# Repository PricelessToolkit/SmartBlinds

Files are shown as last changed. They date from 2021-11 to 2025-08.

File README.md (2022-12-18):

# Battery Powered Smart Blinds
 
With lithium-ion battery 2500 mA autonomy is 8 months.

## Youtube Video

https://youtu.be/99Hgh3yqyf8

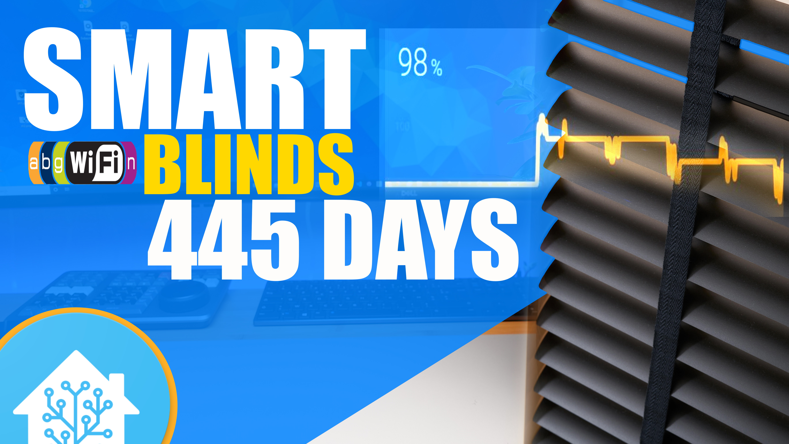
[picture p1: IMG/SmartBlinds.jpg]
SmartBlinds (https://youtu.be/99Hgh3yqyf8)


### Want to support me ? Subscribe and like!

# Update

15.11.2021 - v2 board, I added D5,D6,D7 pins for manual control."not tested" 
the board has become a little bigger, it will not fit into the case. You need to change the 3d model.

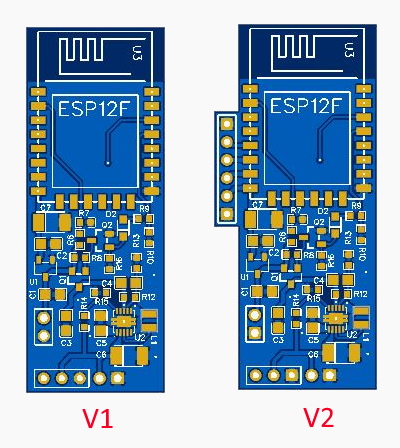
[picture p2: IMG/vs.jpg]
SmartBlinds
[]

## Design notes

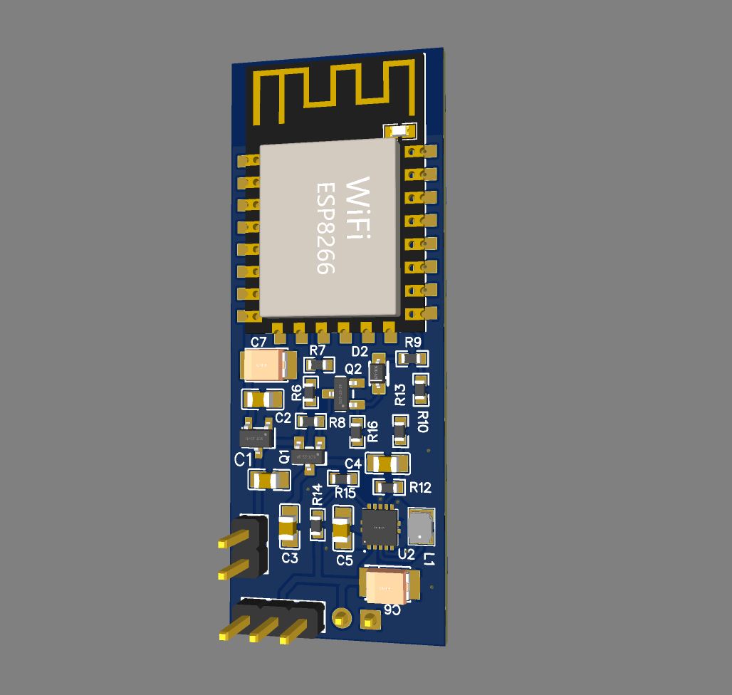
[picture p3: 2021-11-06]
IMG/v1.JPG

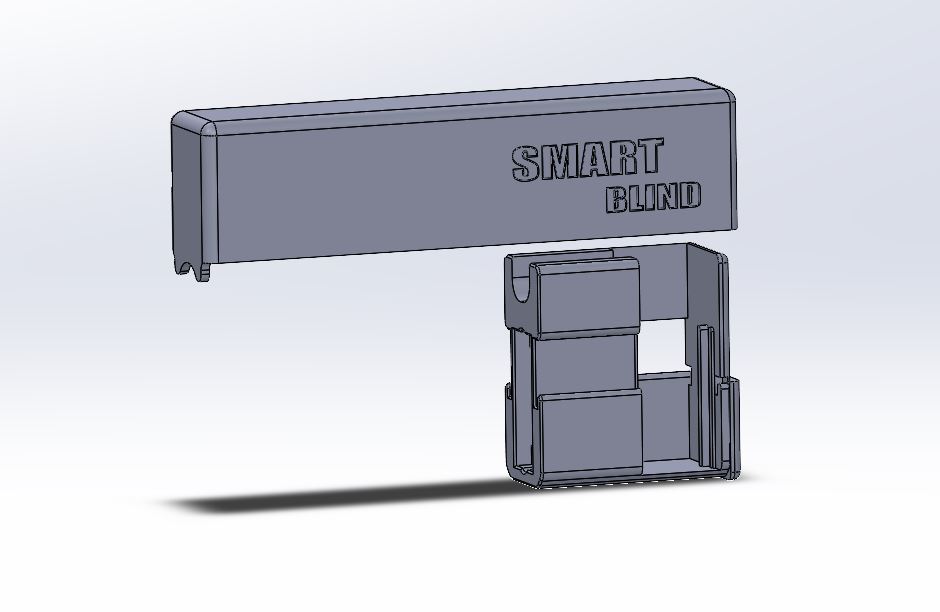
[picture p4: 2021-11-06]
IMG/SB.JPG

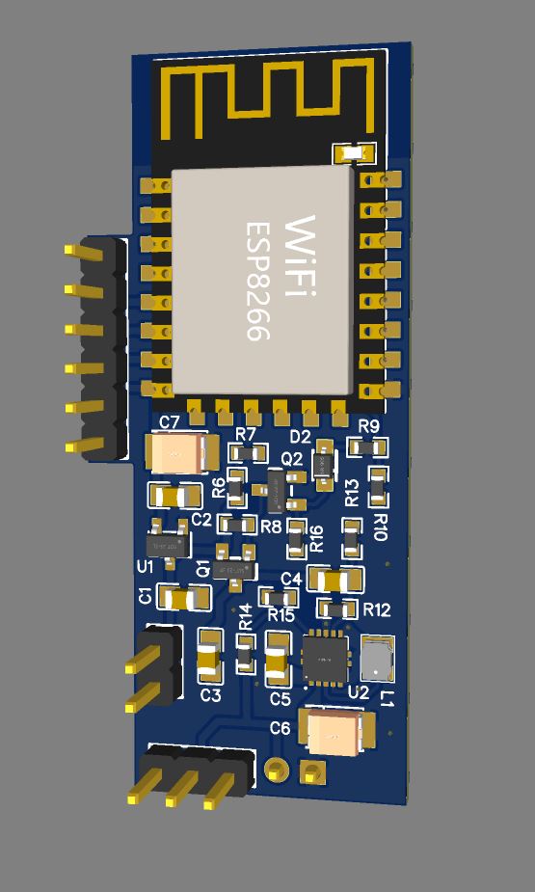
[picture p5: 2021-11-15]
IMG/v2.JPG

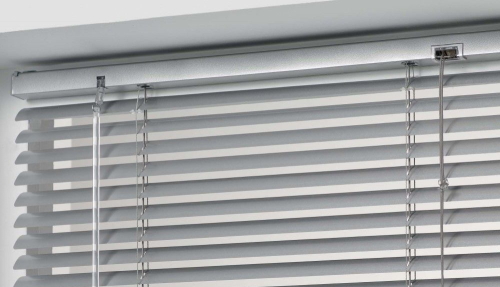
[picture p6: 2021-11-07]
IMG/Blinds.jpg

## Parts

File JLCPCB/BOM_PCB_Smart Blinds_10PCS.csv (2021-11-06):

ID | Name | Designator | Footprint | Quantity | Manufacturer Part | Manufacturer | Supplier | Supplier Part | Price | Pins | 3DModel | Assembly Type | JLCPCB Part Class | JLCPCB SMD | LCSC Assembly | Paste Type | Contributor | SMT Type | image | link
2 | 10k | R1,R2,R3,R4,R5,R9 | R0603 | 60 | RTT03103JTP | RALEC | LCSC | C103210 | 0.001 | 2 | R0603_L1.6-W0.8-H0.8 |  |  |  |  |  | LCEDA_Lib |  |  | https://www.mouser.in/datasheet/2/447/PYu_RT_1_to_0_01_RoHS_L_11-1669912.pdf
3 | TS342A2P-WZ | PROG,RST | SW-SMD_L4.0-W2.9-LS5.0 | 20 | TS342A2P-WZ | SHOU HAN | LCSC | C557591 | 0.041 | 2 |  |  | Extended Part |  |  |  | LCSC |  |  | https://item.szlcsc.com/330471.html
4 | ESP-12F(ESP8266MOD) | U3 | WIFIM-SMD_ESP-12F-ESP8266MOD | 10 | ESP-12F(ESP8266MOD) | Ai-Thinker | LCSC | C82891 | 1.482 | 22 | WIFIM-SMD_WIFI-L24.0-W16.0-H3.1 |  | Extended Part |  |  |  | 立创EDA官方封装库 |  |  | https://item.szlcsc.com/84052.html
5 | 10uf | C7 | CASE-B_3528 | 10 | T491A226K006AT | KEMET | LCSC | C118989 | 0.129 | 2 | CASE-B_L3.5-W2.8-H1.9 |  |  |  |  |  | LCEDA_Lib |  |  | https://img.jlc.com/pdf/applyPasteComponent/2021-05-29/507681S/b3196547ade04cd291a1b09ea1ee2ece/C7199_22UF.PDF
6 | 100nF | C2,C1 | C0805 | 20 | C0805B104M500NT | 火炬 | LCSC | C515949 | 0.007 | 2 | C0805_L2.0-W1.3-H1.3 |  |  |  |  |  | LCEDA_Lib |  |  | https://item.szlcsc.com/373011.html
7 | 10uF | C3 | C0805 | 10 | GRM155R61A106ME21D | Murata Electronics | LCSC | C324476 | 0.021 | 2 | C0805_L2.0-W1.3-H1.3 |  |  |  |  |  | LCEDA_Lib |  |  | https://item.szlcsc.com/373011.html
8 | 0.1uF | C4,C5 | C0805 | 20 | C0805B104M500NT | 火炬 | LCSC | C515949 | 0.007 | 2 | C0805_L2.0-W1.3-H1.3 |  |  |  |  |  | LCEDA_Lib |  |  | https://item.szlcsc.com/373011.html
9 | 1N5819 | D2 | SOD-323_L1.8-W1.3-LS2.5-RD | 10 | 1N5819WS(SL) | KEXIN | LCSC | C489147 | 0.026 | 2 | SOD-323_L1.7-W1.3-H1.1-LS2.5 |  |  |  |  |  | LCSC |  |  | https://item.szlcsc.com/295156.html
10 | 4.7uH | L1 | IND-SMD_L2.5-W2.0_WPN2520X | 10 | WPN252010H4R7MT | Sunlord | LCSC | C97033 | 0.061 | 2 | IND-SMD_L2.5-W2.0-H1.0_WPN2520X |  | Extended Part |  |  |  | 立创EDA官方封装库 |  |  | https://item.szlcsc.com/98236.html
11 | AO3401A | Q1 | SOT-23_L2.9-W1.3-P1.90-LS2.4-BR | 10 | AO3401A | AOS | LCSC | C15127 | 0.161 | 3 | SOT-23-3P_L2.9-W1.3-H1.0-LS2.4-P0.95 | smtWeld |  | Yes |  | base | 官方封装库 | Basic | //image.lceda.cn/szlcsc/C15127.jpg | https://item.szlcsc.com/236142.html
12 | 2n3904S | Q2 | SOT-23-3_L2.9-W1.3-P1.90-LS2.4-TR | 10 | 2n3904S-RTK/PS | KEC | LCSC | C18536 | 0.014 | 3 | SOT-23-3P_L2.9-W1.3-H1.0-LS2.4-P0.95 | smtWeld |  | Yes | Yes | expand | 立创EDA官方封装库 | Extend | //image.lceda.cn/szlcsc/C18536.jpg | https://item.szlcsc.com/70837.html
13 | 100k | R6,R8,R16 | R0603 | 30 | RTT03104JTP | RALEC | LCSC | C103211 | 0.001 | 2 | R0603_L1.6-W0.8-H0.8 |  |  |  |  |  | LCEDA_Lib |  |  | https://www.mouser.in/datasheet/2/447/PYu_RT_1_to_0_01_RoHS_L_11-1669912.pdf
14 | 20k | R7 | R0603 | 10 | RTT03203JTP | RALEC | LCSC | C103397 | 0.003 | 2 | R0603_L1.6-W0.8-H0.8 |  |  |  |  |  | LCEDA_Lib |  |  | https://www.mouser.in/datasheet/2/447/PYu_RT_1_to_0_01_RoHS_L_11-1669912.pdf
15 | 220k | R10,R13,R15 | R0603 | 30 | RTT03224JTP | RALEC | LCSC | C103427 | 0.002 | 2 | R0603_L1.6-W0.8-H0.8 |  |  |  |  |  | LCEDA_Lib |  |  | https://www.mouser.in/datasheet/2/447/PYu_RT_1_to_0_01_RoHS_L_11-1669912.pdf
16 | 2M | R12,R14 | R0603 | 20 | RTT03205JTP | RALEC | LCSC | C103403 | 0.001 | 2 | R0603_L1.6-W0.8-H0.8 |  |  |  |  |  | LCEDA_Lib |  |  | https://www.mouser.in/datasheet/2/447/PYu_RT_1_to_0_01_RoHS_L_11-1669912.pdf
18 | MCP1700T-3302E/TT | U1 | SOT-23-3_L2.9-W1.6-P1.90-LS2.8-BR | 10 | MCP1700T-3302E/TT | MICROCHIP | LCSC | C39051 | 0.303 | 3 | SOT-23-3L_L2.9-W1.6-H1.1-LS2.8-P0.95 |  | Extended Part |  |  |  | jiaowoxiaolu |  |  | https://item.szlcsc.com/14454.html
19 | TPS61200DRCR | U2 | VSON-10_L3.0-W3.0-P0.50-TL-EP_TPS62410DRCR | 10 | TPS61200DRCR | Texas Instruments | LCSC | C140320 | 1.361 | 11 | VSON-10_L3.0-W3.0-H0.6-P0.50_TPS |  | Extended Part |  |  |  | LCSC |  |  | https://item.szlcsc.com/55588.html
20 | 22uf | C6 | CASE-B_3528 | 10 | T491A226K006AT | KEMET | LCSC | C118989 | 0.129 | 2 | CASE-B_L3.5-W2.8-H1.9 |  |  |  |  |  | LCEDA_Lib |  |  | https://img.jlc.com/pdf/applyPasteComponent/2021-05-29/507681S/b3196547ade04cd291a1b09ea1ee2ece/C7199_22UF.PDF

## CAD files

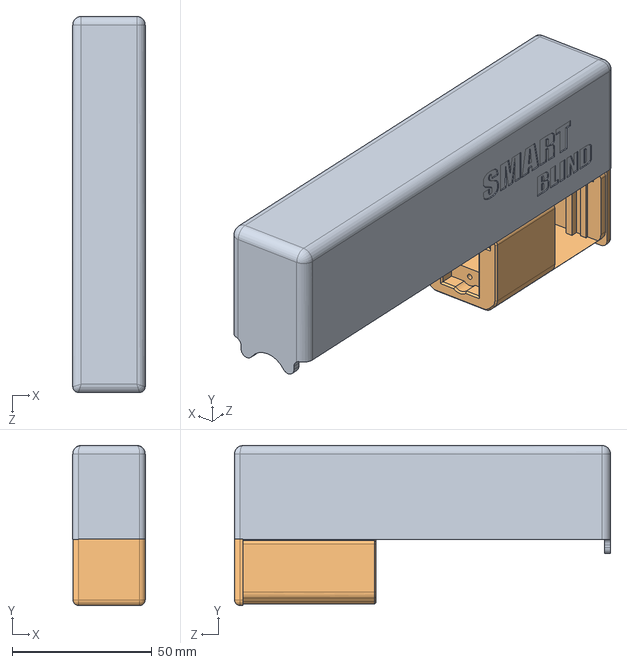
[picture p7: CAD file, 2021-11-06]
3D/SOLIDWORKS/Assem1.SLDASM
25.9 x 57.2 x 134.3 mm
Batterry_Cover
Servo

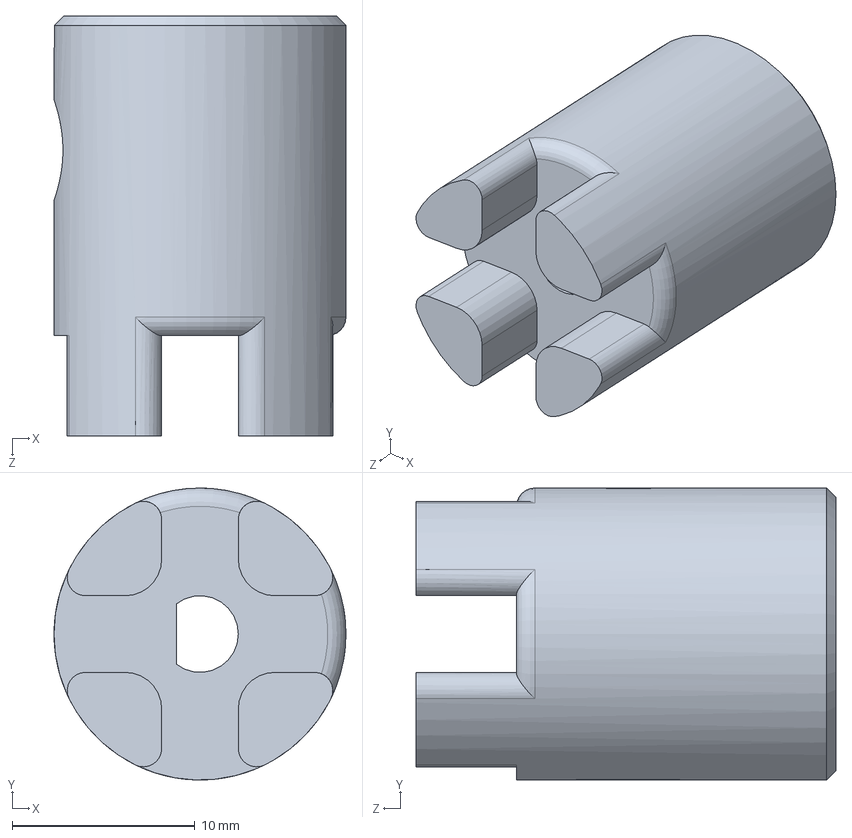
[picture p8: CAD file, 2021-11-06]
3D/SOLIDWORKS/Cupler.SLDPRT
16.0 x 16.0 x 23.0 mm

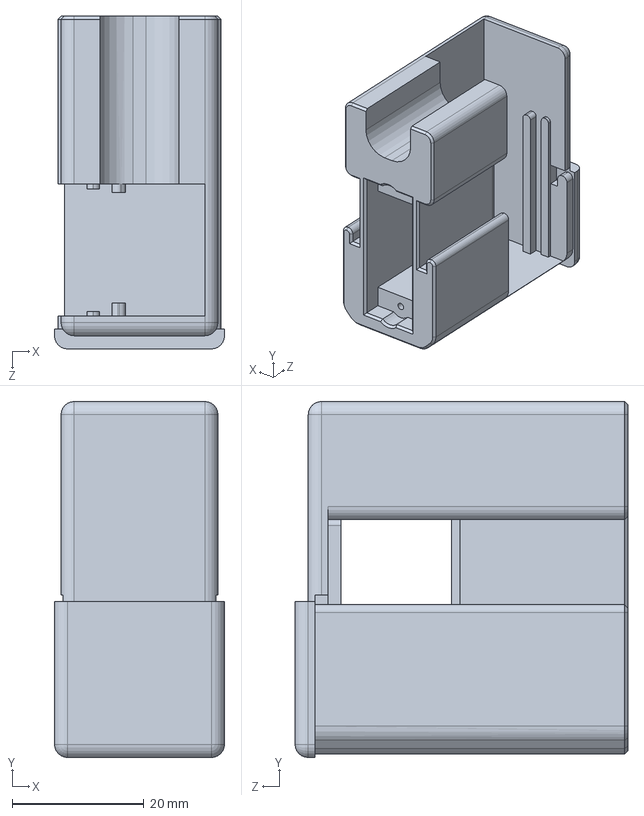
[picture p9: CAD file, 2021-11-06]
3D/SOLIDWORKS/Servo.SLDPRT
25.8 x 54.0 x 50.5 mm

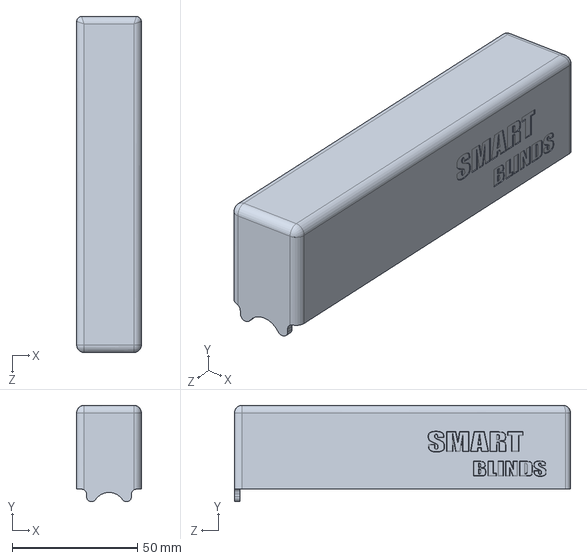
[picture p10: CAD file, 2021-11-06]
3D/SOLIDWORKS/Batterry_Cover.SLDPRT
25.9 x 38.5 x 134.3 mm

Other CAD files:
3D/STL/Cupler.STL
3D/STL/Servo.STL

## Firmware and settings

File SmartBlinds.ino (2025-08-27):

/* Smart Blind (ESP8266) — lean debug + boot state publish
 * - Fast Wi-Fi connect (fixed BSSID + channel + static IP)
 * - Timings: Wi-Fi + MQTT connect durations
 * - Publishes current Position (0–100%) on boot from RTC
 * - Accepts PositionSet (0–100%), converts to 0–180° servo (0°=closed, 180°=open)
 * - Deep sleep after command or after 5 s with no command
 */

#include <ESP8266WiFi.h>
#include <WiFiClient.h>
#include <PubSubClient.h>
#include <Servo.h>

// ===== Wi-Fi (fast-connect) =====
#define STASSID "Change-This"
#define STAPSK  "Change-This"
uint8_t home_mac[6] = { 0x94, 0xA6, 0x7E, 0x94, 0x9B, 0x81 };
int channel = 1;
const char* ssid     = STASSID;
const char* password = STAPSK;

IPAddress local_IP(Change-This);
IPAddress gateway (Change-This);
IPAddress subnet  (Change-This);

// ===== MQTT =====
const char* mqtt_username = "Change-This";
const char* mqtt_password = "Change-This";
const char* mqtt_server   = "Change-This";
const int   mqtt_port     = 1883;

WiFiClient espClient;
PubSubClient client(espClient);

// Topics
const char* TOPIC_BATTERY = "SmartBlinds/Blind-1/Battery";
const char* TOPIC_POS_SET = "SmartBlinds/Blind-1/PositionSet"; // 0..100 (command)
const char* TOPIC_POS     = "SmartBlinds/Blind-1/Position";    // 0..100 (state)
const char* TOPIC_AVAIL   = "SmartBlinds/Blind-1/availability";
const char* AVAIL_ON  = "online";
const char* AVAIL_OFF = "offline";

// ===== Power / Timing =====
static const uint64_t TimeToSleepUs     = 600ULL * 1000000ULL; // 10 min
static const unsigned long WIFI_TIMEOUT_MS   = 15000UL;
static const unsigned long MQTT_TIMEOUT_MS   = 15000UL;
static const unsigned long MQTT_WAIT_CMD_MS  = 5000UL;

// ===== Hardware =====
Servo servo;
const int ServoPin       = 5;  // D1
const int ServoEnablePin = 4;  // D2 (step-up enable, HIGH=on)

// ===== RTC cache =====
struct RtcState {
  uint32_t magic;
  uint32_t angle;     // 0..180
  uint32_t checksum;
};
static const uint32_t RTC_MAGIC = 0xB1A9D501;
static const uint32_t RTC_SLOT  = 65;
static uint32_t rtcChecksum(const RtcState& s) { return (s.magic ^ s.angle) ^ 0xA5A5A5A5; }

// ===== Globals =====
bool commandReceived = false;
unsigned long connectTime = 0;
unsigned long t_boot_ms, t_wifi_begin_ms, t_wifi_connected_ms;
unsigned long t_mqtt_begin_ms, t_mqtt_connected_ms;

// ===== Helpers (fixed mapping: 0%->0°, 100%->180°) =====
static uint8_t angleToPercent(uint32_t a) {
  if (a > 180) a = 180;
  return (uint8_t)((a * 100UL) / 180UL);  // 0° -> 0%, 180° -> 100%
}
static uint32_t percentToAngle(uint8_t p) {
  if (p > 100) p = 100;
  return (uint32_t)((p * 180UL) / 100UL); // 0% -> 0°, 100% -> 180°
}
static void printIp(IPAddress ip) { Serial.printf("%d.%d.%d.%d", ip[0], ip[1], ip[2], ip[3]); }

void goToSleep(const char* reason) {
  Serial.printf("[SLEEP] %lus — %s\n", (unsigned long)(TimeToSleepUs / 1000000ULL), reason);
  digitalWrite(ServoEnablePin, LOW);
  servo.detach();
  if (client.connected()) client.disconnect();
  WiFi.disconnect(true);
  WiFi.mode(WIFI_OFF);
  delay(10);
  Serial.flush();
  ESP.deepSleep(TimeToSleepUs, WAKE_RF_DEFAULT);
}

// Publish availability + current Position (from RTC) at boot
void publishInitialState() {
  client.publish(TOPIC_AVAIL, AVAIL_ON, true);

  RtcState st{};
  ESP.rtcUserMemoryRead(RTC_SLOT, (uint32_t*)&st, sizeof(st));
  bool ok = (st.magic == RTC_MAGIC) && (st.checksum == rtcChecksum(st));
  uint8_t pos = ok ? angleToPercent(st.angle) : 0;
  client.publish(TOPIC_POS, String(pos).c_str(), true);
}

void setup() {
  Serial.begin(115200);
  Serial.println();
  Serial.println("=== SMART BLIND BOOT ===");
  t_boot_ms = millis();

  pinMode(ServoEnablePin, OUTPUT);
  digitalWrite(ServoEnablePin, LOW);
  servo.attach(ServoPin);

  WiFi.persistent(false);
  WiFi.config(local_IP, gateway, subnet);
  WiFi.mode(WIFI_STA);

  t_wifi_begin_ms = millis();
  WiFi.begin(ssid, password, channel, home_mac, true);

  unsigned long wifiStart = millis();
  Serial.println("[WiFi] Connecting...");
  while (WiFi.status() != WL_CONNECTED) {
    if (millis() - wifiStart >= WIFI_TIMEOUT_MS) goToSleep("Wi-Fi timeout");
    delay(10);
    yield();
  }
  t_wifi_connected_ms = millis();
  Serial.print("[WiFi] Connected. IP: "); printIp(WiFi.localIP());
  Serial.printf("  RSSI: %d dBm  (dur %lums)\n", WiFi.RSSI(), t_wifi_connected_ms - t_wifi_begin_ms);

  client.setServer(mqtt_server, mqtt_port);
  client.setKeepAlive(10);
  client.setSocketTimeout(5);
  client.setBufferSize(512);
  client.setCallback(mqttCallback);

  mqttReconnect();           // connect + subscribe
  publishInitialState();     // availability + current position (retained)
  connectTime = millis();    // start short wait window
  Serial.println("[INFO] Ready for PositionSet (0–100).");
}

void mqttReconnect() {
  t_mqtt_begin_ms = millis();
  unsigned long start = millis();
  while (!client.connected()) {
    if (millis() - start >= MQTT_TIMEOUT_MS) goToSleep("MQTT timeout");

    String clientId = "SmartBlind-" + String(ESP.getChipId(), HEX);
    Serial.printf("[MQTT] Connecting as %s ...\n", clientId.c_str());

    bool ok = client.connect(
      clientId.c_str(),
      mqtt_username, mqtt_password,
      TOPIC_AVAIL, 0, true, AVAIL_OFF
    );

    if (ok) {
      t_mqtt_connected_ms = millis();
      Serial.printf("[MQTT] Connected. (dur %lums, boot→MQTT %lums)\n",
                    t_mqtt_connected_ms - t_mqtt_begin_ms,
                    t_mqtt_connected_ms - t_boot_ms);

      // Battery (retained)
      int raw = analogRead(A0);
      raw = constrain(raw, 554, 750);
      int battPct = map(raw, 554, 750, 0, 100);
      battPct = constrain(battPct, 0, 100);
      client.publish(TOPIC_BATTERY, String(battPct).c_str(), true);

      client.subscribe(TOPIC_POS_SET); // listen for 0..100%
    } else {
      delay(100);
      yield();
    }
  }
}

// Handle PositionSet (0..100) -> move servo 0..180
void mqttCallback(char* topic, byte* payload, unsigned int length) {
  if (String(topic) != TOPIC_POS_SET) return;
  commandReceived = true;

  String msg; msg.reserve(length);
  for (unsigned int i = 0; i < length; i++) msg += (char)payload[i];
  uint8_t percent = (uint8_t)constrain(msg.toInt(), 0, 100);
  uint32_t desiredAngle = percentToAngle(percent);
  Serial.printf("[CMD] %u%% -> %lu°\n", percent, desiredAngle);

  // Read last angle
  RtcState st{};
  ESP.rtcUserMemoryRead(RTC_SLOT, (uint32_t*)&st, sizeof(st));
  bool rtcValid = (st.magic == RTC_MAGIC) && (st.checksum == rtcChecksum(st));
  uint32_t lastAngle = rtcValid ? st.angle : 255;
  Serial.printf("[RTC] valid=%s last=%lu°\n", rtcValid ? "YES" : "NO", lastAngle);

  if (lastAngle != desiredAngle) {
    Serial.println("[SERVO] Enable rail + move");
    digitalWrite(ServoEnablePin, HIGH);
    delay(120);
    servo.write(desiredAngle);
    delay(250);
    digitalWrite(ServoEnablePin, LOW);
    Serial.println("[SERVO] Done, rail off");

    st.magic = RTC_MAGIC;
    st.angle = desiredAngle;
    st.checksum = rtcChecksum(st);
    ESP.rtcUserMemoryWrite(RTC_SLOT, (uint32_t*)&st, sizeof(st));
  } else {
    Serial.println("[SERVO] Same angle, skip");
  }

  // Publish final position so HA reflects it
  uint8_t currentPos = angleToPercent(desiredAngle);
  client.publish(TOPIC_POS, String(currentPos).c_str(), true);

  goToSleep("command handled");
}

void loop() {
  if (!client.connected()) mqttReconnect();
  client.loop();

  // Short window to catch retained or quick manual commands
  if (!commandReceived && (millis() - connectTime > MQTT_WAIT_CMD_MS)) {
    goToSleep("no command");
  }
}
